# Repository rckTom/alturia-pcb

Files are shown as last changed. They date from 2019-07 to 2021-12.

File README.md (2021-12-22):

# Alturia PCB

This repository contains all data to build the hardware of the Alturia rocket flight computer. 

## Features
-  STM32F303CC CPU (48Kb Ram, 256Kb internal Flash)
-  MS5607 Barometric pressure sensor
-  BMI088 IMU (Acceleration: +-24g, rotational rate: +-2000°/s)
-  AIS2120SXTR high acceleration sensor (+-120g)
-  64 Megabyte external flash for logging and configuration data
-  Reverse polarity protection
-  4 x Pyro output channels with max 25A current
-  2 x PWM connector for servos
-  USB (CDC-ACM, Mass Storage and DFU)

## Getting Started

The board is built with [Kicad](http://kicad.org/). Version 5.2 or newer is required. The firmware is located at [alturia-firmware](https://github.com/rckTom/alturia-firmware)

## Board Versions
*   v1.0 rev.B *Initial Board Design*
*   v1.1 rev.A *Fix wrongly connected Crystal*
*   v1.1 rev.B *Fix swaped Pins of the speaker mosfet*

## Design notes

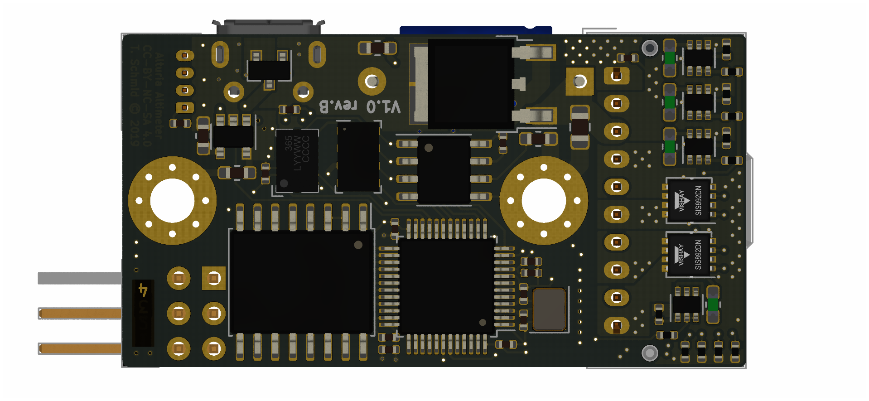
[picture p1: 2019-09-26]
alturia_bottom.png

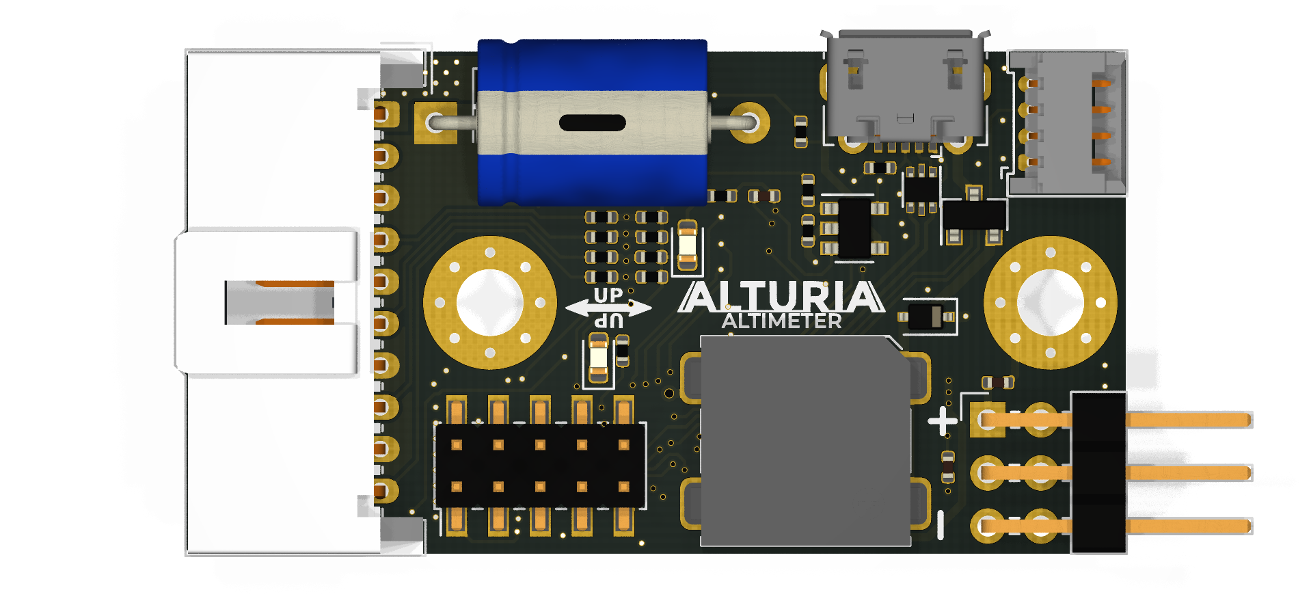
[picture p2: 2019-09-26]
alturia_top.png

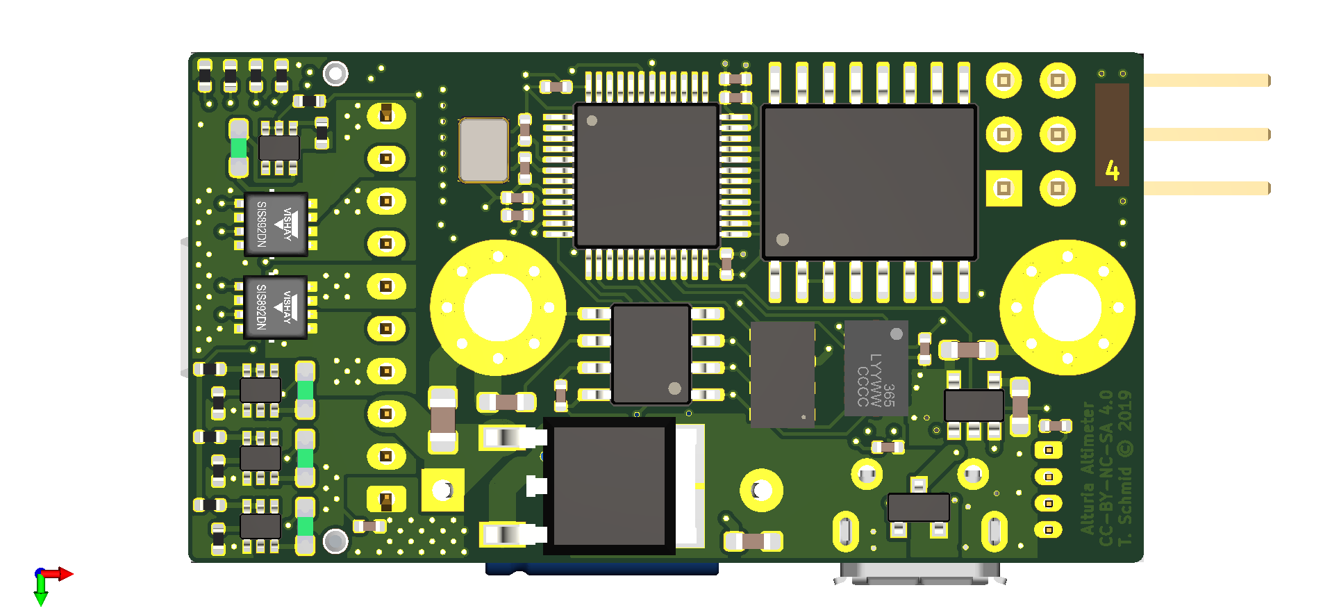
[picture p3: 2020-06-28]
bottom.png

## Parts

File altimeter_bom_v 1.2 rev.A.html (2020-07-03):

Source File | /home/thomas/Projects/altimeter/alturia-pcb/altimeter.sch
BoM Date | So 28 Jun 2020 17:37:28 CEST
Schematic Version | v 1.2 rev.A
Schematic Date
PCB Variant | ['default']
KiCad Version | Eeschema 5.1.6
Component Groups | 44
Component Count (per PCB) | 97
Fitted Components (per PCB) | 97
Number of PCBs | 1
Total Component Count (for 1 PCBs) | 97
 | Description | Part | References | Value | Footprint | Quantity Per PCB | Datasheet | Mouser_Link | Parnumber
1 | Unpolarized capacitor, small symbol | C_Small | C1 C2 C106 C109 C110 C111 C112 C113 C114 C115 C116 C201 C202 C203 C204 C205 | 100n | C_0402_1005Metric | 16 | ~ | https://www.mouser.de/ProductDetail/Wurth-Elektronik/885012205037 | 885012205037
2 | Unpolarized capacitor, small symbol | C_Small | C101 C102 | 14p | C_0402_1005Metric | 2 | ~ | https://www.mouser.de/ProductDetail/Murata-Electronics/GCM1555G1H220JA16D | GCM1555G1H220JA16D
3 | Polarized capacitor | CP | C3 | 1m | CP_Axial_L11.0mm_D8.0mm_P15.00mm_Horizontal | 1 | ~ | https://www.mouser.de/ProductDetail/Illinois-Capacitor-CDE/337TTA016M?qs=3tP%252BN51vMXcJjE4PHk19Og%3D%3D | 337TTA016M
4 | Unpolarized capacitor, small symbol | C_Small | C103 | 1u | C_0603_1608Metric_Pad1.05x0.95mm_HandSolder | 1 | ~ | https://www.mouser.de/ProductDetail/Yageo/CC0603KRX5R8BB105 | CC0603KRX5R8BB105
5 | Unpolarized capacitor, small symbol | C_Small | C119 | 1u | C_0805_2012Metric | 1 | ~ | https://www.mouser.de/ProductDetail/Taiyo-Yuden/UMF212B7105KGHT?qs=%252B6g0mu59x7KoF6NN%2FES6FQ%3D%3D | UMF212B7105KGHT
6 | Unpolarized capacitor, small symbol | C_Small | C108 | 2.2u | C_0603_1608Metric_Pad1.05x0.95mm_HandSolder | 1 | ~ |  | EMK107BJ225MA-T
7 | Unpolarized capacitor, small symbol | C_Small | C117 C118 | 2.2u | C_0402_1005Metric | 2 | ~ | https://www.mouser.de/ProductDetail/Yageo/CC0402KRX5R7BB225?qs=shS2SvXCj6KxdMpn6SQPQQ%3D%3D | CC0402KRX5R7BB225
8 | Unpolarized capacitor, small symbol | C_Small | C104 C120 C121 C122 C123 | 4.7u | C_0805_2012Metric_Pad1.15x1.40mm_HandSolder | 5 | ~ | https://www.mouser.de/ProductDetail/Taiyo-Yuden/GMK212BBJ475KD-T?qs=VWNNG7jHlrJu0gRQmF8TjA%3D%3D | GMK212BBJ475KD-T
9 | Unpolarized capacitor, small symbol | C_Small | C107 | 4.7u | C_0805_2012Metric | 1 | ~ | https://www.mouser.de/ProductDetail/Taiyo-Yuden/GMK212BBJ475KD-T?qs=VWNNG7jHlrJu0gRQmF8TjA%3D%3D | GMK212BBJ475KD-T
10 | Unpolarized capacitor, small symbol | C_Small | C124 | 4.7u | C_0603_1608Metric_Pad1.05x0.95mm_HandSolder | 1 | ~ | https://www.mouser.de/ProductDetail/Murata-Electronics/GRM188R60J475KE19D?qs=8N7GLiuM2OS81roWI9UfgQ%3D%3D | GRM188R60J475KE19D
11 | 75V 0.15A Fast switching Diode, SOD-323 | 1N4148WS | D103 | 1N4148WS | D_SOD-323 | 1 | https://www.vishay.com/docs/85751/1n4148ws.pdf | https://www.mouser.de/ProductDetail/ON-Semiconductor-Fairchild/1N4148WS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 | 1N4148WS
12 | RGB LED, red/green/blue/anode | LED_RGBA | D101 | LED_RGBA | SMD_RGB_LED | 1 | https://www.mouser.de/datasheet/2/445/150080M153000-1714255.pdf | https://www.mouser.de/ProductDetail/Wurth-Elektronik/150080M153000 | 150080M153000
13 | Resettable fuse, polymeric positive temperature coefficient | Polyfuse | F1 F301 F401 F501 | Polyfuse | Fuse_0603_1608Metric_Pad1.05x0.95mm_HandSolder | 4 | ~ | https://www.mouser.de/ProductDetail/Bel-Fuse/0ZCM0008FF2G | 0ZCM0008FF2G
14 | Generic connector, single row, 01x04, script generated (kicad-library-utils/schlib/autogen/connector/) | Conn_01x04 | J205 | Conn_01x04 | Molex_PicoBlade_53048-0410_1x04_P1.25mm_Horizontal | 1 | ~ | https://www.mouser.de/ProductDetail/Molex/53048-0410 | 53048-0410
15 | Generic connector, single row, 01x10, script generated (kicad-library-utils/schlib/autogen/connector/) | Conn_01x10 | J201 | Conn_01x10 | Molex_MicroClasp_55935-1010_1x10_P2.00mm_Horizontal | 1 | ~ | https://www.mouser.de/ProductDetail/Molex/55935-1010 | 55935-1010
16 | Generic connectable mounting pin connector, single row, 01x10, script generated (kicad-library-utils/schlib/autogen/connector/) | Conn_01x10_MountingPin | J206 | Conn_01x10_MountingPin | Molex_PicoBlade_53398-1071_1x10-1MP_P1.25mm_Vertical | 1 | ~ | https://www.mouser.de/ProductDetail/Molex/53398-1071 | 53398-1071
17 | Generic connector, double row, 02x03, odd/even pin numbering scheme (row 1 odd numbers, row 2 even numbers), script generated (kicad-library-utils/schlib/autogen/connector/) | Conn_02x03_Odd_Even | J203 | Conn_02x03_Counter_Clockwise | PinHeader_2x03_P2.54mm_Horizontal | 1 | ~ | https://www.mouser.de/ProductDetail/Harwin/M20-9740346 | M20-9740346
18 | Cortex Debug Connector, standard ARM Cortex-M SWD and JTAG interface | Conn_ARM_JTAG_SWD_10 | J202 | Conn_ARM_JTAG_SWD_10 | PinHeader_2x05_P2.00mm_Vertical_SMD | 1 | http://infocenter.arm.com/help/topic/com.arm.doc.ddi0314h/DDI0314H_coresight_components_trm.pdf | https://www.mouser.de/ProductDetail/Amphenol-FCI/57202-G51-05LF | 57202-G51-05LF
19 | USB Micro Type B connector | USB_B_Micro | J204 | USB_B_Micro | USB_Micro-B_Molex-105017-0001 | 1 | ~ | https://www.mouser.de/ProductDetail/Molex/105017-0001 | 105017-0001
20 | Crystal speaker/transducer | Speaker_Crystal | LS101 | Speaker_Crystal | CSS-95B30-SMT | 1 | https://www.mouser.de/datasheet/2/670/css-95b30-smt-1311901.pdf | https://www.mouser.de/ProductDetail/CUI/CSS-95B30-SMT-TR | CSS-95B30-SMT-TR
21 | 100mA IC, 45V Vce, Dual NPN/NPN Transistors, SOT-363 | BC847BDW1 | Q1 Q301 Q401 Q501 | BC848CDW1T1G | SOT-363_SC-70-6 | 4 | http://www.onsemi.com/pub_link/Collateral/BC846BDW1T1-D.PDF | https://www.mouser.de/manufacturer/on-semiconductor/ | BC848CDW1T1G
22 | P-MOSFET transistor, gate/source/drain | Q_PMOS_GSD | Q101 | DMG2301L | SOT-23 | 1 | ~ | https://www.mouser.de/ProductDetail/Diodes-Incorporated/DMG2301L-7 | DMG2301L-7
23 | N-MOSFET transistor, gate/source/drain | Q_NMOS_GSD | Q102 | NTR4003NT1G | SOT-23 | 1 | ~ | https://www.mouser.de/ProductDetail/ON-Semiconductor/NTR4003NT1G | NTR4003NT1G
24 | P-MOSFET transistor, drain/gate/source | SI7149ADP | Q103 | SISS05dn | Vishay_PowerPAK_1212-8_Single | 1 | https://www.mouser.de/datasheet/2/427/siss05dn-1595673.pdf | https://www.mouser.de/ProductDetail/Vishay-Siliconix/SISS05DN-T1-GE3 | SISS05DN-T1-GE3
25 | Resistor, small symbol | R_Small | R201 | 1.5k | R_0402_1005Metric | 1 | ~ | https://www.mouser.de/ProductDetail/Vishay-Dale/CRCW04021K50FKED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 | CRCW04021K50FKEDC
26 | Resistor, small symbol | R_Small | R103 R104 | 100k | R_0402_1005Metric | 2 | ~ | https://www.mouser.de/ProductDetail/Vishay-Dale/CRCW0402100KFKED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 | CRCW0402100KFKEDC
27 | Resistor | R | R202 | 120 | R_0603_1608Metric_Pad1.05x0.95mm_HandSolder | 1 | ~ | https://www.mouser.de/datasheet/2/315/AOA0000C304-1149620.pdf | ERJ-6RBD1200V
28 | Resistor | R | R10 R13 R102 R106 R108 R301 R303 R401 R403 R501 R503 | 2.7k | R_0402_1005Metric | 11 | ~ | https://www.mouser.de/ProductDetail/Vishay-Dale/CRCW04022K70FKEDC | CRCW04022K70FKEDC
29 | Resistor | R | R2 R4 R6 R8 R11 | 220k | R_0402_1005Metric | 5 | ~ | https://www.mouser.de/ProductDetail/Vishay-Dale/CRCW0402220KFKED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 | CRCW0402220KFKEDC
30 | Resistor | R | R12 R302 R402 R502 | 33 | R_0402_1005Metric | 4 | ~ | https://www.mouser.de/ProductDetail/TE-Connectivity-Neohm/CPF0402B33RE1 | CPF0402B33RE1
31 | Resistor | R | R101 R105 R107 R109 | 680 | R_0402_1005Metric | 4 | ~ | https://www.mouser.de/ProductDetail/Vishay-Dale/CRCW0402680RFKED | CRCW0402680RFKEDC
32 | Resistor | R | R1 R3 R5 R7 R9 | 68k | R_0402_1005Metric | 5 | ~ | https://www.mouser.de/ProductDetail/Vishay-Dale/CRCW0402768K0FKEDC | CRCW040268K0FKEDC
33 |  | AIS2120SXTR | U103 | AIS2120SXTR | SOIC-8_3.9x4.9mm_P1.27mm | 1 |  | https://www.mouser.de/ProductDetail/STMicroelectronics/AIS2120SXTR | AIS2120SXTR
34 |  | ATA6561 | U202 | ATA6561 | DFN-8-1EP_3x3mm_P0.65mm_EP1.55x2.4mm | 1 | http://ww1.microchip.com/downloads/en/DeviceDoc/20005991B.pdf | https://www.mouser.de/ProductDetail/Microchip-Technology/ATA6561-GBQW-N | ATA6561-GBQW-N
35 |  | BMI088 | U106 | BMI088 | BMI088 | 1 |  | https://www.mouser.de/ProductDetail/Bosch-Sensortec/BMI088 | BMI088
36 |  | LDL212 | U105 | LDL212 | DFN-6-1EP_3x3mm_P0.95mm_EP1.7x2.6mm | 1 | https://www.st.com/resource/en/datasheet/ldl212.pdf | https://www.mouser.de/ProductDetail/STMicroelectronics/LDL212PU50R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 | LDL212PU50R
37 | Single General-Purpose Low-Voltage Comparator, SOT-23-5/SC-70-5 | LMV331 | U1 | LMV331 | SOT-353_SC-70-5 | 1 | http://www.ti.com/lit/ds/symlink/lmv331.pdf | https://www.mouser.de/datasheet/2/115/LMV331_393-335820.pdf | LMV331SE-7
38 | Barometric pressure sensor, 10cm resolution, 10 to 1200 mbar, I2C and SPI interface up to 20MHz, LGA-8 | MS5611-01BA | U107 | MS5611-01BA | LGA-8_3x5mm_P1.25mm | 1 | https://www.te.com/commerce/DocumentDelivery/DDEController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 | https://www.mouser.de/ProductDetail/Measurement-Specialties/MS560702BA03-50 | MS560702BA03-50
39 |  | MT25Q_W9 | U102 | MT25Q_W9 | micron-wpdfn_8x6mm | 1 | https://www.micron.com/-/media/client/global/documents/products/data-sheet/nor-flash/serial-nor/mt25q/die-rev-b/mt25q_qlkt_l_512_abb_0.pdf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 | https://www.mouser.de/ProductDetail/Micron/MT25QL512ABB1EW9-0SIT | MT25QL512ABB1EW9-0SIT
40 |  | SI7232DN | U301 U501 | SI7232DN | Vishay_PowerPAK_1212-8_Dual | 2 |  | https://www.mouser.de/ProductDetail/Vishay-Siliconix/SI7232DN-T1-GE3 | SI7232DN-T1-GE3
41 | ARM Cortex-M4 MCU, 1024KB flash, 128KB RAM, 168MHz, 1.8-3.6V, 51 GPIO, LQFP-64 | STM32F405RGTx | U108 | STM32F405RGTx | LQFP-64_10x10mm_P0.5mm | 1 | http://www.st.com/st-web-ui/static/active/en/resource/technical/document/datasheet/DM00037051.pdf | https://www.mouser.de/ProductDetail/STMicroelectronics/STM32F405RGT7?qs=sGAEpiMZZMvh0aGzCjJ9ppxwOvp%252BLF2Y | STM32F405RGT7
42 |  | TLV767 | U101 | TLV767 | TI_WSON_TLV767 | 1 | http://www.ti.com/lit/ds/symlink/tlv767.pdf?HQS=TI-null-null-mousermode-df-pf-null-wwe&DCM=yes&distId=26 | https://www.mouser.de/Texas-Instruments/Semiconductors/Power-Management-ICs/Voltage-Regulators-Voltage-Controllers/LDO-Voltage-Regulators/TLV767-Series/_/N-5c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 | TLV76733DRVR
43 |  | USBLC6-2SC6-Power_Protection | U201 | USBLC6-2P6 | SOT-666 | 1 | http://www2.st.com/resource/en/datasheet/CD00050750.pdf | https://www.mouser.de/ProductDetail/STMicroelectronics/USBLC6-2SC6 | USBLC6-2SC6
44 | Four pin crystal, GND on pins 2 and 4 | Crystal_GND24 | Y1 | Crystal_GND24 | Crystal_SMD_2016-4Pin_2.0x1.6mm | 1 | https://www.mouser.de/datasheet/2/122/ECX-1637B-1633271.pdf | https://www.mouser.de/ProductDetail/ECS/ECS-160-12-37B-CTN-TR | ECS-160-12-37B-CTN-TR

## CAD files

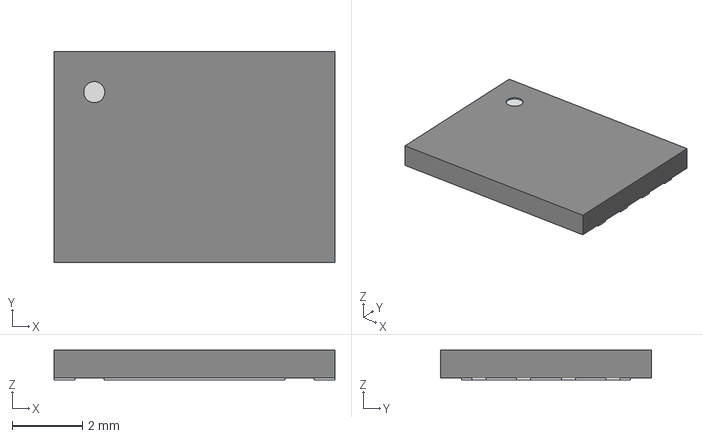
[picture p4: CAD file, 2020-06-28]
3d-models/wdfn8_5x6.step
8.00 x 6.00 x 0.85 mm

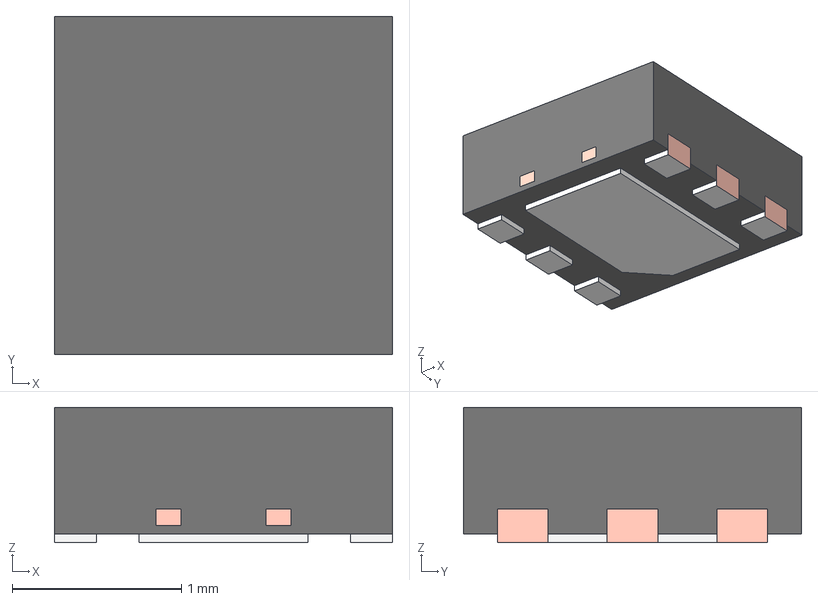
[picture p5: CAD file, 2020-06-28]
3d-models/DRV0006B.stp
2.00 x 2.00 x 0.8 mm
BODY-SON
FRAME-DRV0006B
PIN1-ID

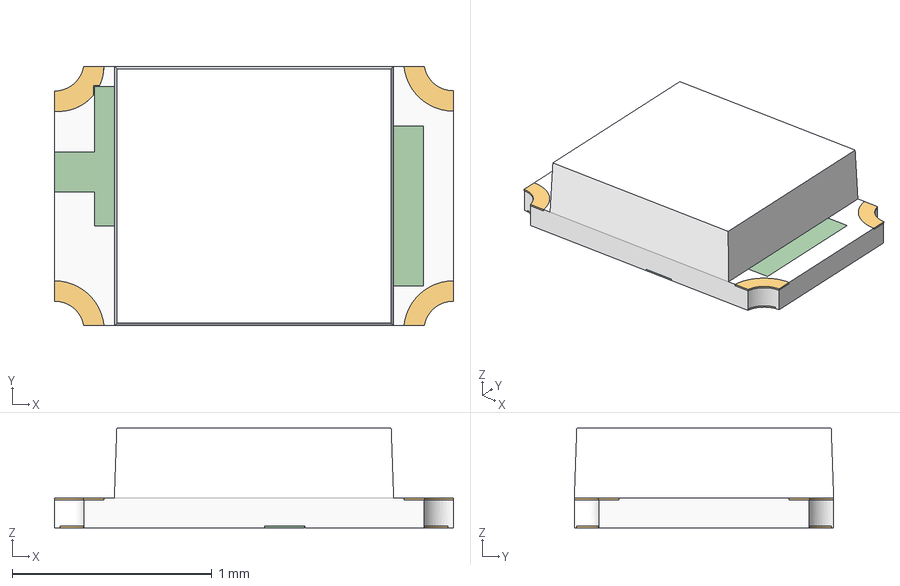
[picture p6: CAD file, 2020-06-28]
3d-models/Download_STP_WL-SFCD-0805_rev1.stp
2.00 x 1.30 x 0.5 mm
Pins x 15

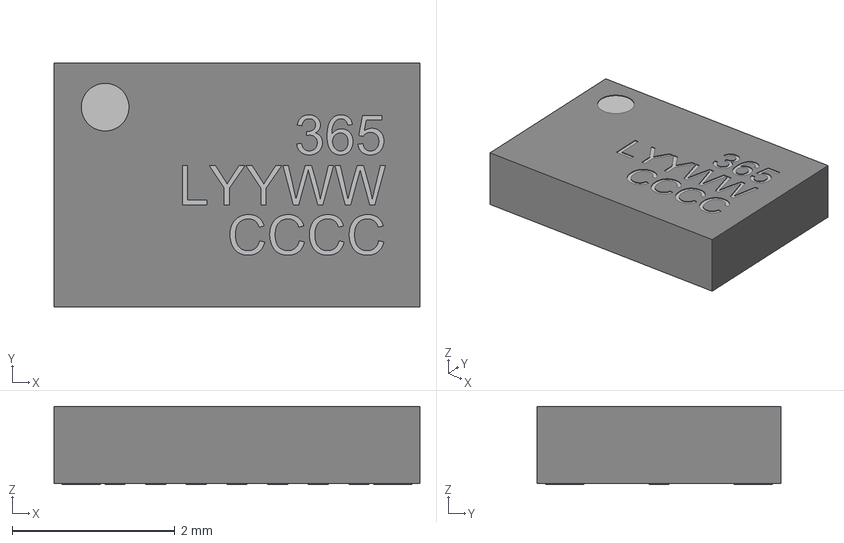
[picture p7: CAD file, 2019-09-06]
3d-models/bmi_088.stp
4.50 x 3.00 x 0.96 mm

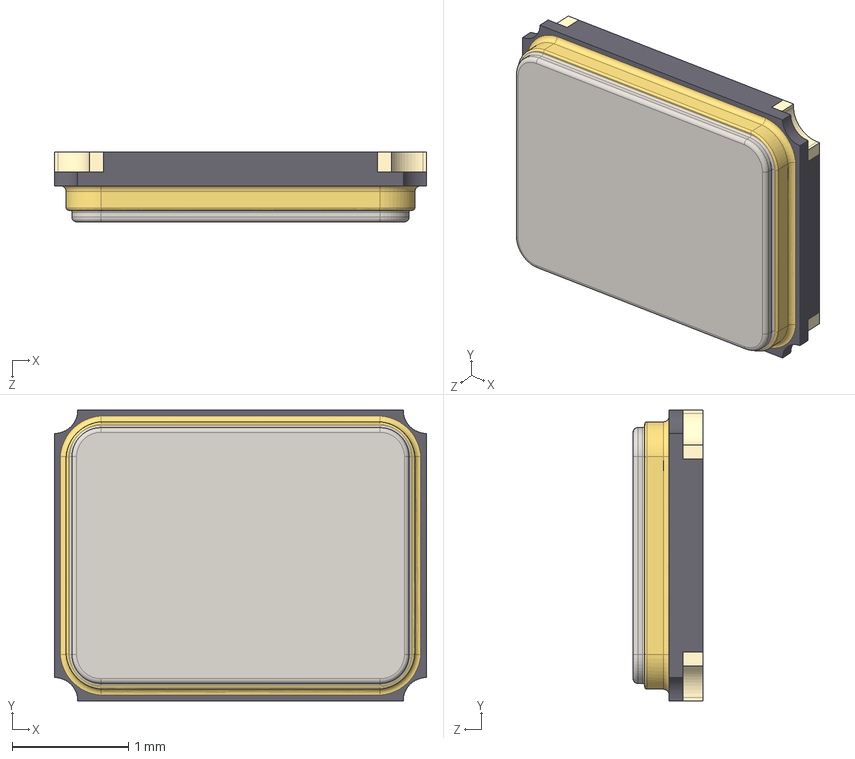
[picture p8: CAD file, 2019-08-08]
3d-models/User Library-tsx-3225.step
3.20 x 2.50 x 0.6 mm

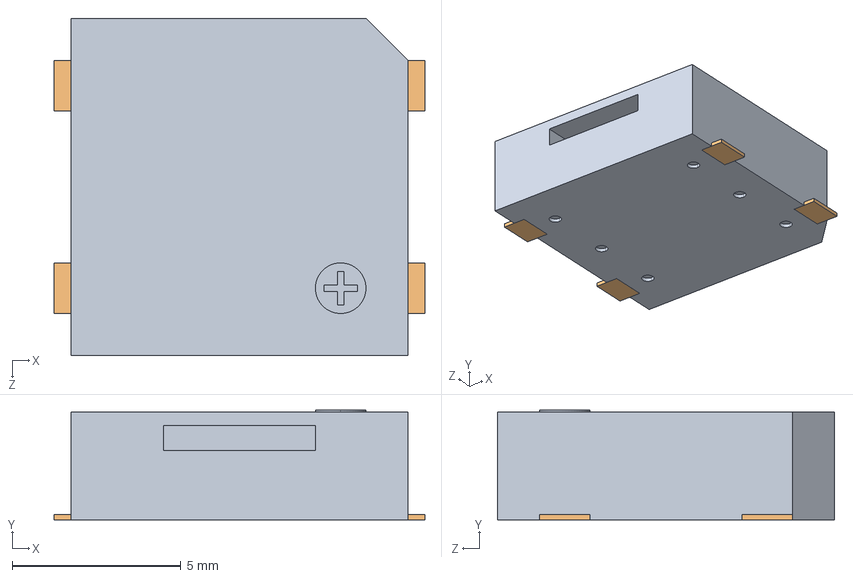
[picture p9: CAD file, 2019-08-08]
3d-models/CUI_CSS-95B30-SMT.step
11.0 x 3.25 x 10.0 mm

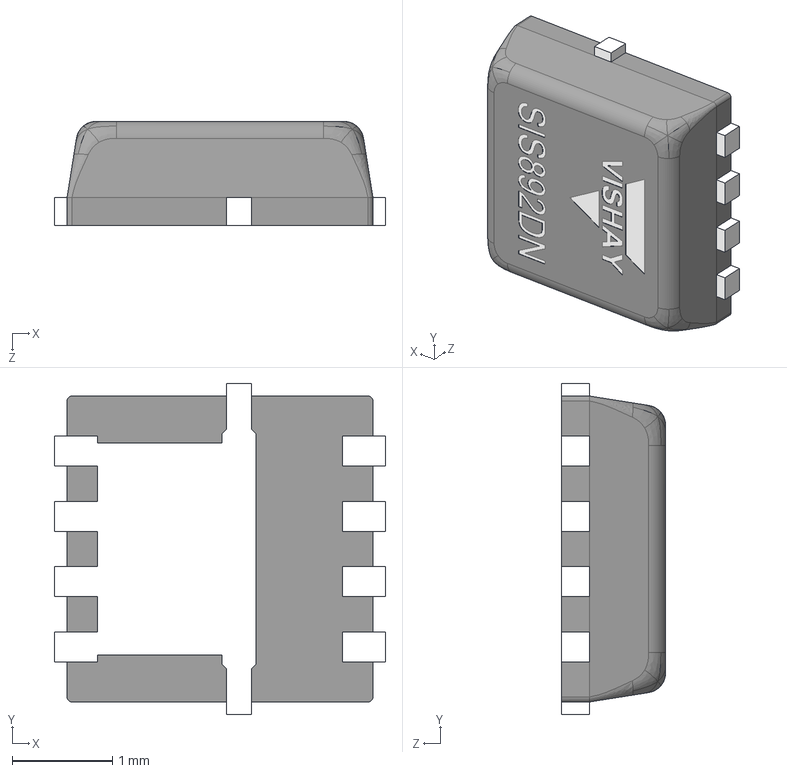
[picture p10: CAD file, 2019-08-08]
3d-models/User Library-PowerPAK 1212-8-SiS892DN.step
3.30 x 3.30 x 1.04 mm

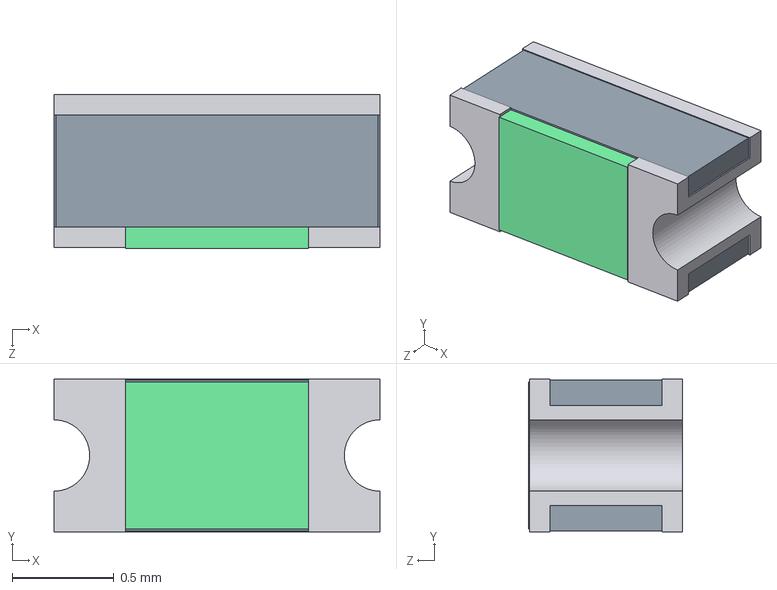
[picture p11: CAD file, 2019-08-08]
3d-models/User Library-ptc06032-1.step
1.60 x 0.75 x 0.755 mm

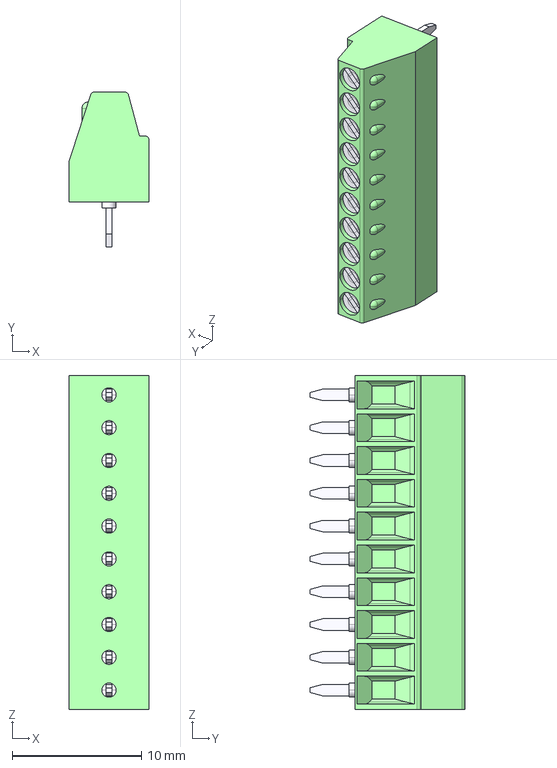
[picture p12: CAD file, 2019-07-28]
3d-models/pxc_1725737_05_MPT-0-5-10-2-54_3D.stp
6.20 x 12.0 x 25.9 mm

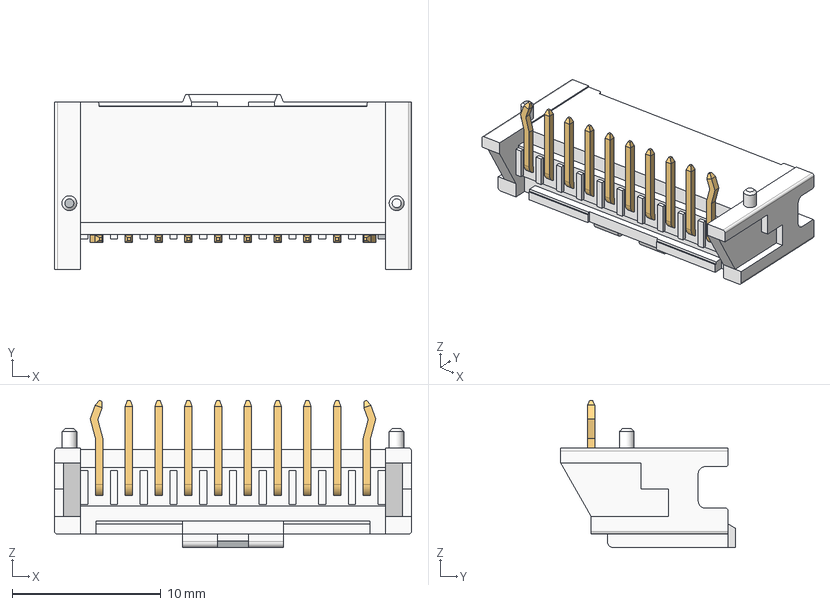
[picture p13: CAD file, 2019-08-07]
3d-models/559351010.stp
24.0 x 11.8 x 9.90 mm

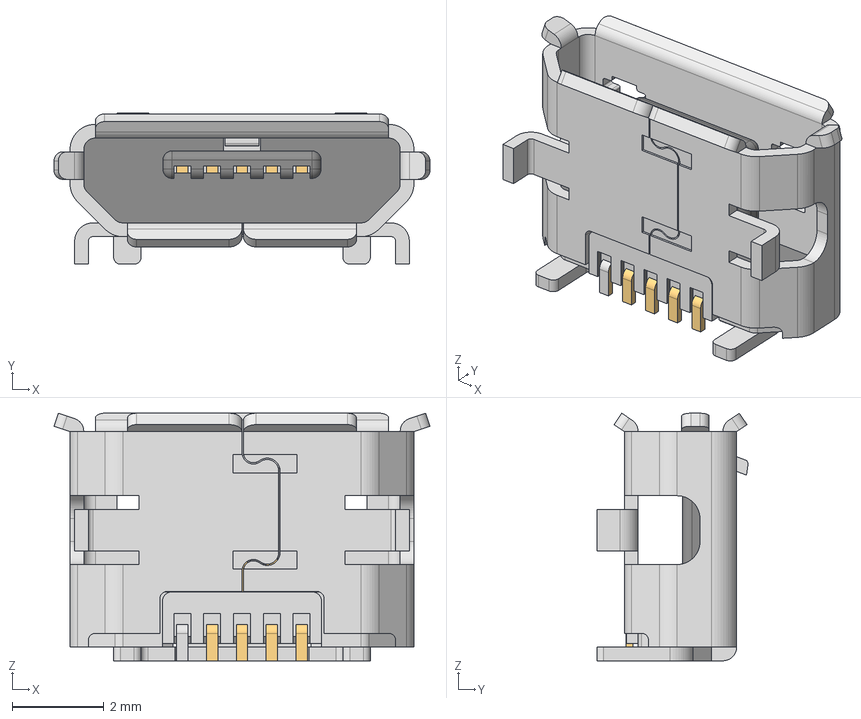
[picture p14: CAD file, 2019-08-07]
3d-models/1050170001.stp
8.20 x 3.30 x 5.40 mm

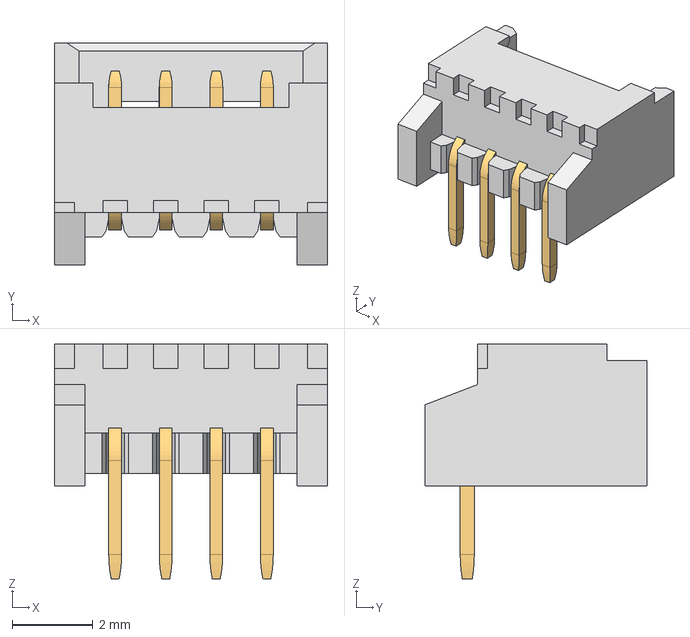
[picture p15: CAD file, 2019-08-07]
3d-models/530480410.stp
6.75 x 5.50 x 5.80 mm

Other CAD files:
3d-models/wdfn8_5x6.FCStd
3d-models/wdfn8_5x6.obj

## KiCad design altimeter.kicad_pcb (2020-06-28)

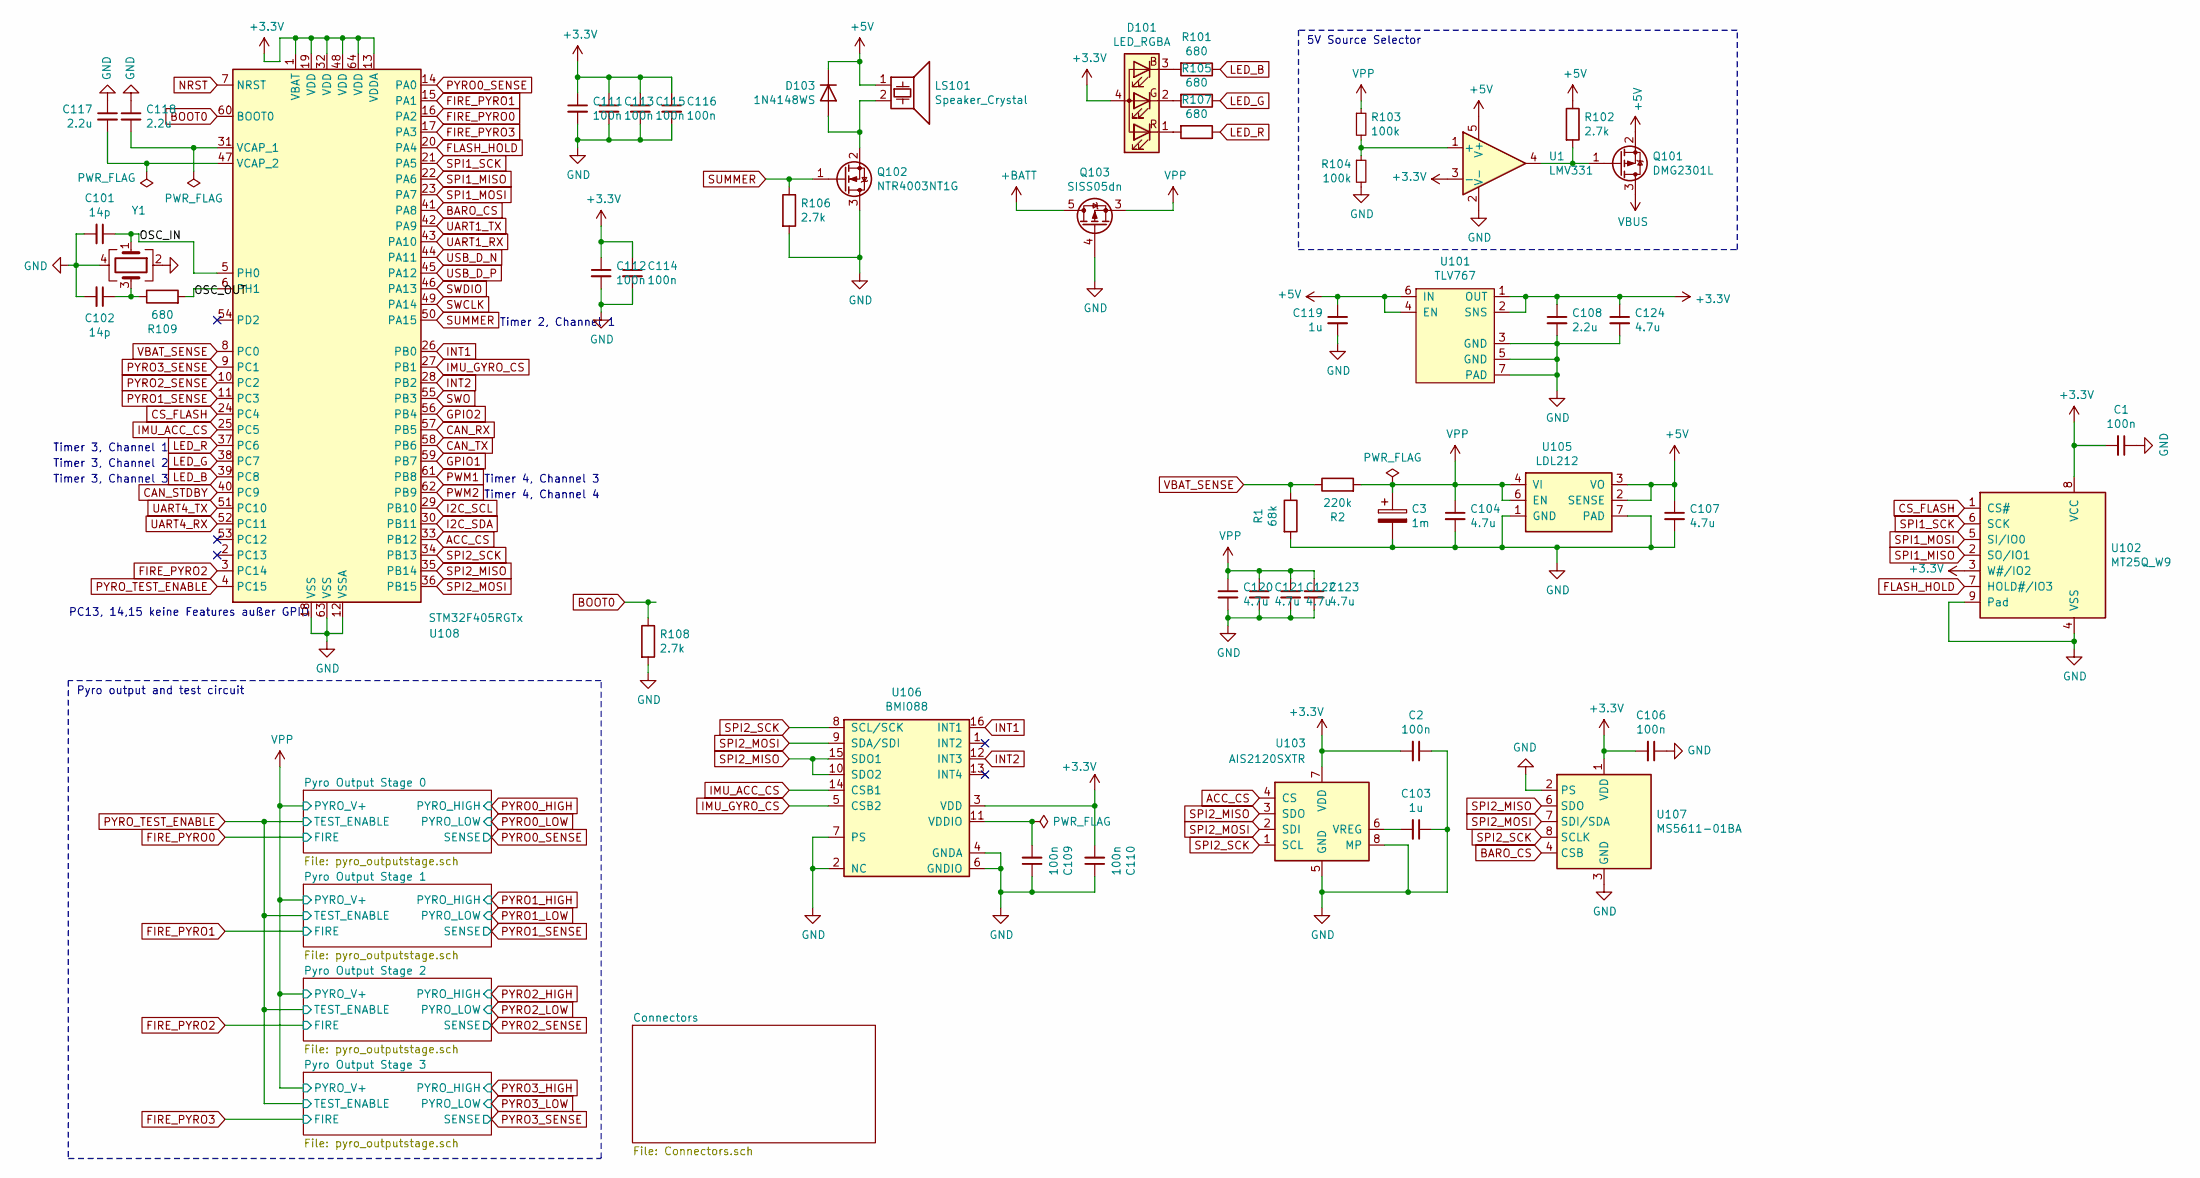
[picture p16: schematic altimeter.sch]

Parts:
C1, C2, C106, C109, C110, C111, C112, C113, C114, C115, C116: 100n; C_0402_1005Metric
C3: 1m; CP_Axial_L11.0mm_D8.0mm_P15.00mm_Horizontal
C101, C102: 14p; C_0402_1005Metric
C103: 1u; C_0603_1608Metric_Pad1.05x0.95mm_HandSolder
C104, C120, C121, C122, C123: 4.7u; C_0805_2012Metric_Pad1.15x1.40mm_HandSolder
C107: 4.7u; C_0805_2012Metric
C108: 2.2u; C_0603_1608Metric_Pad1.05x0.95mm_HandSolder
C117, C118: 2.2u; C_0402_1005Metric
C119: 1u; C_0805_2012Metric
C124: 4.7u; C_0603_1608Metric_Pad1.05x0.95mm_HandSolder
D101: LED_RGBA; SMD_RGB_LED
D103: 1N4148WS; D_SOD-323
LS101: Speaker_Crystal; CSS-95B30-SMT
Q101: DMG2301L; SOT-23
Q102: NTR4003NT1G; SOT-23
Q103: SISS05dn; Vishay_PowerPAK_1212-8_Single
R1: 68k; R_0402_1005Metric
R2: 220k; R_0402_1005Metric
R101, R105, R107, R109: 680; R_0402_1005Metric
R102, R106, R108: 2.7k; R_0402_1005Metric
R103, R104: 100k; R_0402_1005Metric
U1: LMV331; SOT-353_SC-70-5
U101: TLV767; TI_WSON_TLV767
U102: MT25Q_W9; micron-wpdfn_8x6mm
U103: AIS2120SXTR; SOIC-8_3.9x4.9mm_P1.27mm
U105: LDL212; DFN-6-1EP_3x3mm_P0.95mm_EP1.7x2.6mm
U106: BMI088
U107: MS5611-01BA; LGA-8_3x5mm_P1.25mm
U108: STM32F405RGTx; LQFP-64_10x10mm_P0.5mm
Y1: Crystal_GND24; Crystal_SMD_2016-4Pin_2.0x1.6mm

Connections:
+3V3: C1.2, C2.2, C106.2, C108.1, C110.2, C111.1, C112.1, C113.1, C114.1, C115.1, C116.1, C124.1, D101.4 (A), U1.3 (-), U101.1 (OUT), U101.2 (SNS), U102.3 (W#/IO2), U102.8 (VCC), U103.7 (VDD), U106.3 (VDD), U107.1 (VDD), U108.1 (VBAT), U108.13 (VDDA), U108.19 (VDD), U108.32 (VDD), U108.48 (VDD), U108.64 (VDD); also elsewhere on the board
+5V: C107.1, C119.1, D103.1 (K), LS101.1, Q101.2 (S), R102.1, U1.5 (V+), U101.4 (EN), U101.6 (IN), U105.2 (SENSE), U105.3 (VO); also elsewhere on the board
+BATT: Q103.5 (D); also elsewhere on the board
/OSC_IN: C101.1, U108.5 (PH0), Y1.1
/OSC_OUT: R109.2, U108.6 (PH1)
ACC_CS: U103.4 (CS), U108.33 (PB12)
BARO_CS: U107.4 (CSB), U107.5 (CSB), U108.41 (PA8)
BOOT0: R108.1, U108.60 (BOOT0)
CAN_RX: U108.57 (PB5); also elsewhere on the board
CAN_STDBY: U108.40 (PC9); also elsewhere on the board
CAN_TX: U108.58 (PB6); also elsewhere on the board
CS_FLASH: U102.1 (CS#), U108.24 (PC4)
FIRE_PYRO2: U108.3 (PC14); also elsewhere on the board
FIRE_PYRO3: U108.17 (PA3); also elsewhere on the board
FLASH_HOLD: U102.7 (HOLD#/IO3), U108.20 (PA4)
GND: C1.1, C2.1, C3.2, C101.2, C102.2, C103.1, C104.2, C106.1, C107.2, C108.2, C109.1, C110.1, C111.2, C112.2, C113.2, C114.2, C115.2, C116.2, C117.1, C118.1, C119.2, C120.2, C121.2, C122.2, C123.2, C124.2, Q102.3 (D), Q103.4 (G), R1.2, R104.2, R106.2, R108.2, U1.2 (V-), U101.3 (GND), U101.5 (GND), U101.7 (PAD), U102.4 (VSS), U102.9 (Pad), U103.5 (GND), U103.8 (MP), U105.1 (GND), U105.7 (PAD), U106.2 (NC), U106.4 (GNDA), U106.6 (GNDIO), U106.7 (PS), U107.2 (PS), U107.3 (GND), U108.12 (VSSA), U108.18 (VSS), U108.63 (VSS), Y1.2, Y1.4; also elsewhere on the board
GPIO1: U108.59 (PB7); also elsewhere on the board
GPIO2: U108.56 (PB4); also elsewhere on the board
I2C_SCL: U108.29 (PB10); also elsewhere on the board
I2C_SDA: U108.30 (PB11); also elsewhere on the board
IMU_ACC_CS: U106.14 (CSB1), U108.25 (PC5)
IMU_GYRO_CS: U106.5 (CSB2), U108.27 (PB1)
INT1: U106.16 (INT1), U108.26 (PB0)
INT2: U106.12 (INT3), U108.28 (PB2)
LED_B: R101.1, U108.39 (PC8)
LED_G: R105.1, U108.38 (PC7)
LED_R: R107.1, U108.37 (PC6)
NRST: U108.7 (NRST); also elsewhere on the board
unnamed: C102.1, R109.1, Y1.3
unnamed: C103.2, U103.6 (VREG)
unnamed: C109.2, U106.11 (VDDIO)
unnamed: C117.2, U108.47 (VCAP_2)
unnamed: C118.2, U108.31 (VCAP_1)
unnamed: D101.1 (RK), R107.2
unnamed: D101.2 (GK), R105.2
unnamed: D101.3 (BK), R101.2
unnamed: D103.2 (A), LS101.2, Q102.2 (S)
unnamed: Q101.1 (G), R102.2, U1.4
unnamed: R103.2, R104.1, U1.1 (+)
PWM1: U108.61 (PB8); also elsewhere on the board
PWM2: U108.62 (PB9); also elsewhere on the board
PYRO0_SENSE: U108.14 (PA0); also elsewhere on the board
PYRO1_SENSE: U108.11 (PC3); also elsewhere on the board
PYRO2_SENSE: U108.10 (PC2); also elsewhere on the board
PYRO3_SENSE: U108.9 (PC1); also elsewhere on the board
PYRO_TEST_ENABLE: U108.4 (PC15); also elsewhere on the board
SPI1_MISO: U102.2 (SO/IO1), U108.22 (PA6)
SPI1_MOSI: U102.5 (SI/IO0), U108.23 (PA7)
SPI1_SCK: U102.6 (SCK), U108.21 (PA5)
SPI2_MISO: U103.3 (SDO), U106.10 (SDO2), U106.15 (SDO1), U107.6 (SDO), U108.35 (PB14)
SPI2_MOSI: U103.2 (SDI), U106.9 (SDA/SDI), U107.7 (SDI/SDA), U108.36 (PB15)
SPI2_SCK: U103.1 (SCL), U106.8 (SCL/SCK), U107.8 (SCLK), U108.34 (PB13)
SUMMER: Q102.1 (G), R106.1, U108.50 (PA15)
SWCLK: U108.49 (PA14); also elsewhere on the board
SWDIO: U108.46 (PA13); also elsewhere on the board
SWO: U108.55 (PB3); also elsewhere on the board
UART1_RX: U108.43 (PA10); also elsewhere on the board
UART1_TX: U108.42 (PA9); also elsewhere on the board
UART4_RX: U108.52 (PC11); also elsewhere on the board
UART4_TX: U108.51 (PC10); also elsewhere on the board
USB_D_N: U108.44 (PA11); also elsewhere on the board
USB_D_P: U108.45 (PA12); also elsewhere on the board
VBAT_SENSE: R1.1, R2.1, U108.8 (PC0)
VBUS: Q101.3 (D); also elsewhere on the board

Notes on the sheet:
Pyro output and test circuit
5V Source Selector
Timer 4, Channel 4
Timer 4, Channel 3
Timer 3, Channel 1
Timer 3, Channel 2
Timer 3, Channel 3
Timer 2, Channel 1
PC13, 14,15 keine Features außer GPIO

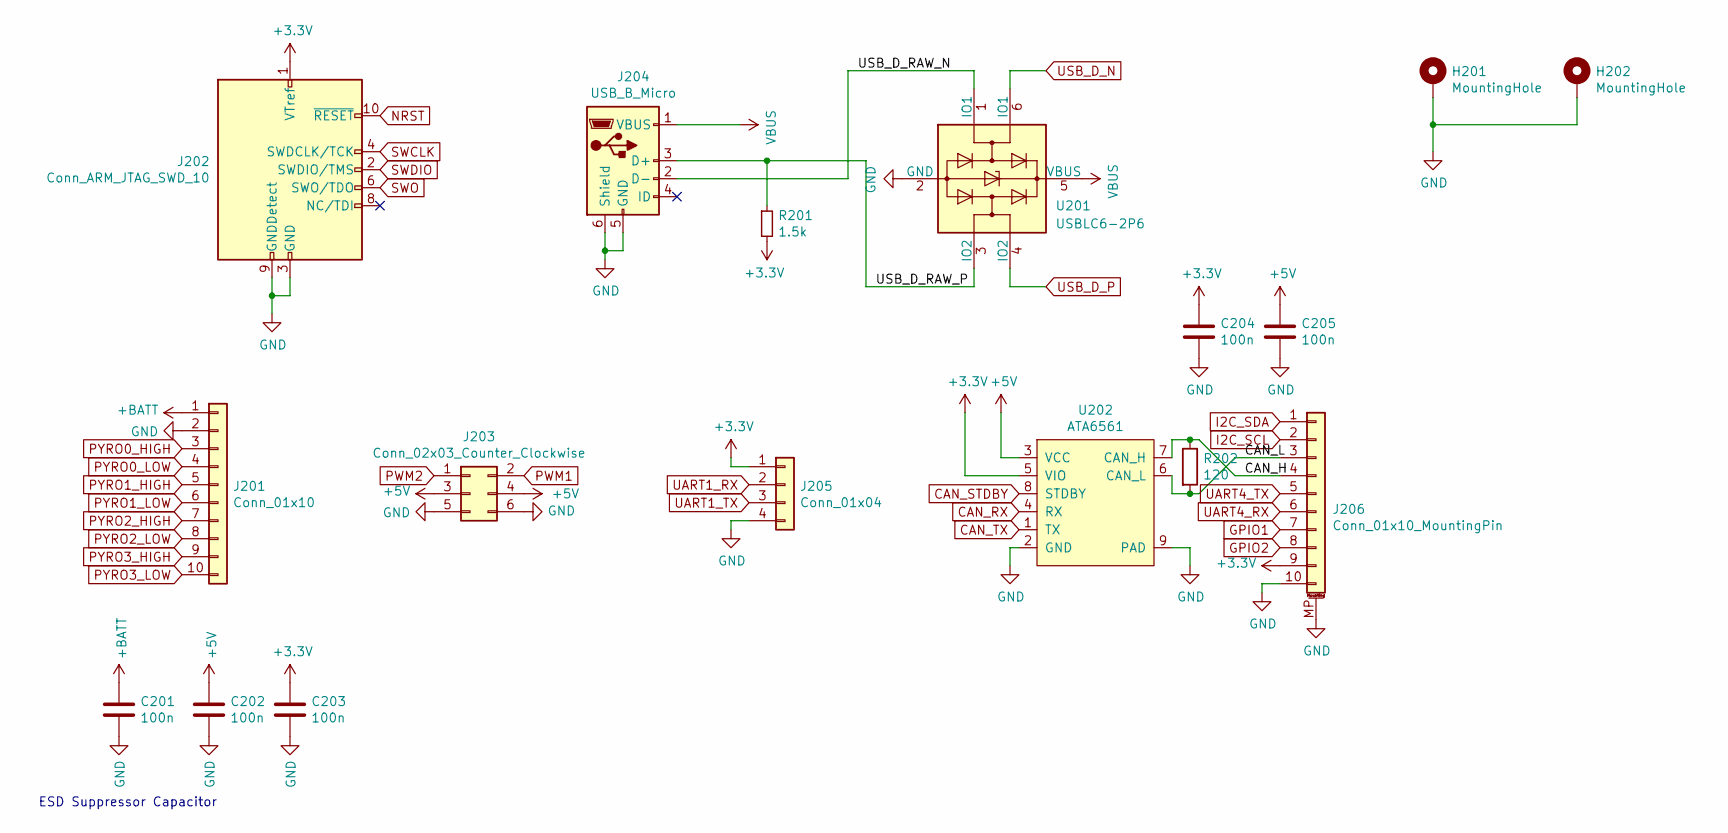
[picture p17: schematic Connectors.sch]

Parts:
C201, C202, C203, C204, C205: 100n; C_0402_1005Metric
H201, H202: MountingHole; MountingHole_3.2mm_M3_Pad_Via
J201: Conn_01x10; Molex_MicroClasp_55935-1010_1x10_P2.00mm_Horizontal
J202: Conn_ARM_JTAG_SWD_10; PinHeader_2x05_P2.00mm_Vertical_SMD
J203: Conn_02x03_Counter_Clockwise; PinHeader_2x03_P2.54mm_Horizontal
J204: USB_B_Micro; USB_Micro-B_Molex-105017-0001
J205: Conn_01x04; Molex_PicoBlade_53048-0410_1x04_P1.25mm_Horizontal
J206: Conn_01x10_MountingPin; Molex_PicoBlade_53398-1071_1x10-1MP_P1.25mm_Vertical
R201: 1.5k; R_0402_1005Metric
R202: 120; R_0603_1608Metric_Pad1.05x0.95mm_HandSolder
U201: USBLC6-2P6; SOT-666
U202: ATA6561; DFN-8-1EP_3x3mm_P0.65mm_EP1.55x2.4mm

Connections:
+3V3: C203.1, C204.1, J202.1 (VTref), J205.1, J206.9, R201.2, U202.5 (VIO); also elsewhere on the board
+5V: C202.1, C205.1, J203.3, J203.4, U202.3 (VCC); also elsewhere on the board
+BATT: C201.1, J201.1; also elsewhere on the board
/Connectors/CAN_H: J206.4, R202.1, U202.7 (CAN_H)
/Connectors/CAN_L: J206.3, R202.2, U202.6 (CAN_L)
/Connectors/USB_D_RAW_N: J204.2 (D-), U201.1 (IO1)
/Connectors/USB_D_RAW_P: J204.3 (D+), R201.1, U201.3 (IO2)
CAN_RX: U202.4 (RX); also elsewhere on the board
CAN_STDBY: U202.8 (STDBY); also elsewhere on the board
CAN_TX: U202.1 (TX); also elsewhere on the board
GND: C201.2, C202.2, C203.2, C204.2, C205.2, H201.1, H202.1, J201.2, J202.3 (GND), J202.5 (GND), J202.9 (GNDDetect), J203.5, J203.6, J204.5 (GND), J204.6 (Shield), J205.4, J206.10, J206.MP (MountPin), U201.2 (GND), U202.2 (GND), U202.9 (PAD); also elsewhere on the board
GPIO1: J206.7; also elsewhere on the board
GPIO2: J206.8; also elsewhere on the board
I2C_SCL: J206.2; also elsewhere on the board
I2C_SDA: J206.1; also elsewhere on the board
NRST: J202.10 (~RESET~); also elsewhere on the board
PWM1: J203.2; also elsewhere on the board
PWM2: J203.1; also elsewhere on the board
PYRO2_LOW: J201.8; also elsewhere on the board
PYRO3_LOW: J201.10; also elsewhere on the board
SWCLK: J202.4 (SWDCLK/TCK); also elsewhere on the board
SWDIO: J202.2 (SWDIO/TMS); also elsewhere on the board
SWO: J202.6 (SWO/TDO); also elsewhere on the board
UART1_RX: J205.2; also elsewhere on the board
UART1_TX: J205.3; also elsewhere on the board
UART4_RX: J206.6; also elsewhere on the board
UART4_TX: J206.5; also elsewhere on the board
USB_D_N: U201.6 (IO1); also elsewhere on the board
USB_D_P: U201.4 (IO2); also elsewhere on the board
VBUS: J204.1 (VBUS), U201.5 (VBUS); also elsewhere on the board

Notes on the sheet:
ESD Suppressor Capacitor

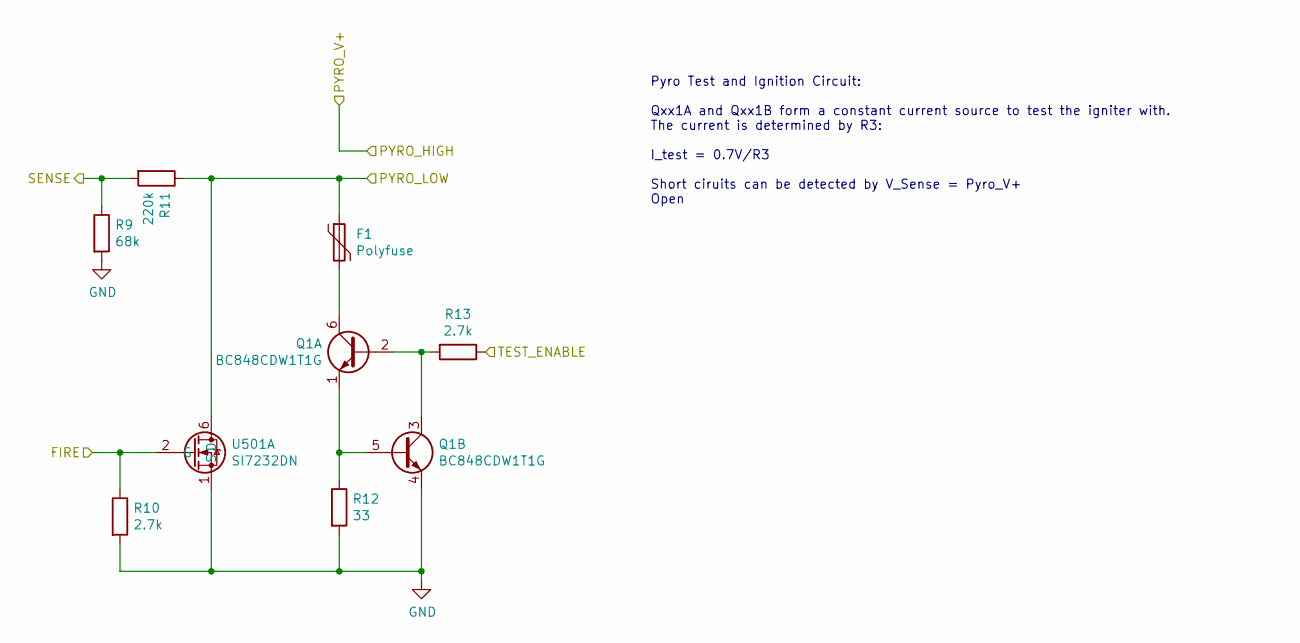
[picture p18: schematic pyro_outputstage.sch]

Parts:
F301: Polyfuse; Fuse_0603_1608Metric_Pad1.05x0.95mm_HandSolder
Q301: BC848CDW1T1G; SOT-363_SC-70-6
R3: 68k; R_0402_1005Metric
R4: 220k; R_0402_1005Metric
R301, R303: 2.7k; R_0402_1005Metric
R302: 33; R_0402_1005Metric
U301: SI7232DN; Vishay_PowerPAK_1212-8_Dual

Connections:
GND: Q301.4 (E2), R3.2, R301.2, R302.2, U301.1 (S), U301.3 (S); also elsewhere on the board
unnamed: F301.2, Q301.6 (C1)
unnamed: Q301.1 (E1), Q301.5 (B2), R302.1
unnamed: Q301.2 (B1), Q301.3 (C2), R303.2
PYRO0_SENSE: R3.1, R4.2; also elsewhere on the board
PYRO_TEST_ENABLE: R303.1; also elsewhere on the board

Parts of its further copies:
F1, F401, F501: Polyfuse; Fuse_0603_1608Metric_Pad1.05x0.95mm_HandSolder
Q1, Q401, Q501: BC848CDW1T1G; SOT-363_SC-70-6
R5, R7, R9: 68k; R_0402_1005Metric
R6, R8, R11: 220k; R_0402_1005Metric
R10, R13, R401, R403, R501, R503: 2.7k; R_0402_1005Metric
R12, R402, R502: 33; R_0402_1005Metric
U501: SI7232DN; Vishay_PowerPAK_1212-8_Dual

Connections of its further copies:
FIRE_PYRO2: R501.1, U501.4 (G); also elsewhere on the board
FIRE_PYRO3: R10.1, U501.2 (G); also elsewhere on the board
GND: Q1.4 (E2), Q401.4 (E2), Q501.4 (E2), R5.2, R7.2, R9.2, R10.2, R12.2, R401.2, R402.2, R501.2, R502.2, U501.1 (S), U501.3 (S); also elsewhere on the board
unnamed: F1.2, Q1.6 (C1)
unnamed: F401.2, Q401.6 (C1)
unnamed: F501.2, Q501.6 (C1)
unnamed: Q1.1 (E1), Q1.5 (B2), R12.1
unnamed: Q1.2 (B1), Q1.3 (C2), R13.2
unnamed: Q401.1 (E1), Q401.5 (B2), R402.1
unnamed: Q401.2 (B1), Q401.3 (C2), R403.2
unnamed: Q501.1 (E1), Q501.5 (B2), R502.1
unnamed: Q501.2 (B1), Q501.3 (C2), R503.2
PYRO1_SENSE: R5.1, R6.2; also elsewhere on the board
PYRO2_LOW: F501.1, R8.1, U501.5 (D); also elsewhere on the board
PYRO2_SENSE: R7.1, R8.2; also elsewhere on the board
PYRO3_LOW: F1.1, R11.1, U501.6 (D); also elsewhere on the board
PYRO3_SENSE: R9.1, R11.2; also elsewhere on the board
PYRO_TEST_ENABLE: R13.1, R403.1, R503.1; also elsewhere on the board

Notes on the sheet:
Pyro Test and Ignition Circuit: Qxx1A and Qxx1B form a constant current source to test the igniter with. The current is determined by R3: I_test = 0.7V/R3 Short ciruits can be detected by V_Sense = Pyro_V+ Open

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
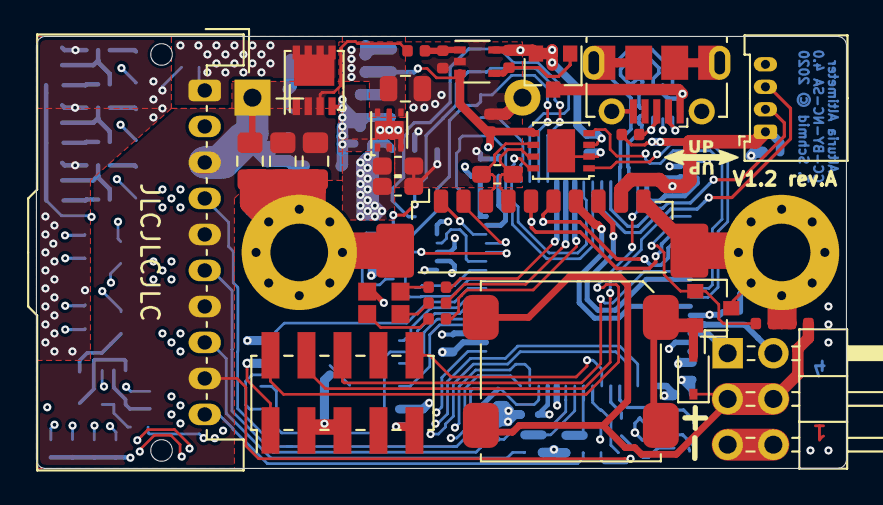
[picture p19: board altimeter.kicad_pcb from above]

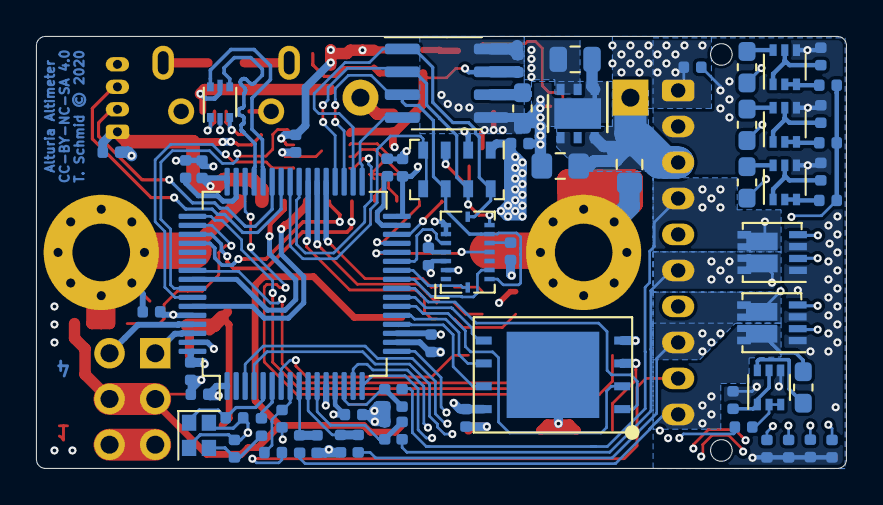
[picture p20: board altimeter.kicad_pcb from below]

Board: 4 copper layers, 45.0 x 24.0 mm, 100 parts (64 on the bottom side), 87 nets.

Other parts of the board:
Ref**: up_arrow

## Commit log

2019-07-28 updates to schematic
    [Connectors.sch, altimeter.kicad_pcb, altimeter.sch]
2019-07-29 add pyro output stages
    [Connectors.sch, altimeter.kicad_pcb, altimeter.sch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]
2019-07-29 increate outline linewidth to conform with the kicad library convention
2019-08-01 update pyro output stage. add a fuse to the test circuit and remove pullup for sense line
    [Connectors.sch, altimeter.sch, pyro_outputstage.sch]
2019-08-07 more work on schematic and layout
    [1050170001.stp, 530480410.stp, 559351010.stp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]
2019-08-08 update to schematic and layout
    [Connectors.sch, User Library-PowerPAK 1212-8-SiS892DN.step, User Library-ptc06032-1.step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]
2019-08-09 flash considerations
    [altimeter.sch]
2019-08-11 major work on layout. nearly finished
    [Connectors.sch, altimeter.kicad_pcb, altimeter.sch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]
2019-08-14 nearly finished with lacout. Added logo
    [Connectors.sch, altimeter.kicad_pcb, altimeter.sch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]
2019-09-04 completed layout
    [Connectors.sch, altimeter.kicad_pcb, altimeter.sch]
2019-09-04 minor updates
    [Connectors.sch, altimeter.kicad_pcb, altimeter.sch]
2019-09-04 first prototyp order
    [altimeter-B_Cu.gbl, altimeter-B_Mask.gbs, altimeter-B_SilkS.gbo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]
2019-09-05 fix untinted vias
    [altimeter-B_Cu.gbl, altimeter-B_Mask.gbs, altimeter-B_SilkS.gbo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]
2019-09-06 changed mcu from stm32f302xc to stm32f303xc
    [altimeter.kicad_pcb, altimeter.sch]
2019-09-06 add some missing mouser links and part numbers to the schematic
    [Connectors.sch, altimeter.sch]
2019-09-06 add missing 3d model for bmi088
    [altimeter.kicad_pcb, bmi_088.stp]
2019-09-26 fix wrong connection of quarz
    [Connectors.sch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]
2019-11-06 swap net names for bmi088 chip select lines
    [altimeter.sch]
2019-11-21 with kicad 5.1.5 the required molex connector is part of the kicad footprint library. Remove custom molex footprints link
2020-05-12 fix swaped gate and source pin of pyro mosfets
    [Connectors.sch, altimeter.kicad_pcb, altimeter.sch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]
2020-05-12 fix servo connectors
    fix pinout of servo connectors. 5V Pin and Signal was swapped
    [Connectors.sch, altimeter.kicad_pcb, pyro_outputstage.sch]
2020-06-28 v1.2 rev A
    [Connectors.sch, DRV0006B.stp, Download_STP_WL-SFCD-0805_rev1.stp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]
2021-12-22 Update README.md
    https://forum.kicad.info/t/warning-avoid-all-links-to-kicad-pcb-org-use-kicad-org/31521

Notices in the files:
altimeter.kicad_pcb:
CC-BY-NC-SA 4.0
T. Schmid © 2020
